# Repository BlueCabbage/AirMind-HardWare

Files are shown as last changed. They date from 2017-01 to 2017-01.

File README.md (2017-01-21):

Hardware
========



PX4 Hardware designs

Website at: http://pixhawk.org

PX4 is an open hardware design, following the OSHW 1.1 definition licensed under the Creative Commons Attribution-ShareAlike 3.0 Unported (CC BY-SA 3.0) license.

Pull requests for relevant fixes are very welcome.

Pixhawk v1 Hardware
===================

FMUv1 & FMUv2 boards

Design files are EAGLE CAD files (can be viewed with the free version)
www.cadsoftusa.com/

And BOM management is performed using Bob Starr's BOM-EX plugin:
http://www.bobstarr.net/pages/downloads.html

Pixhawk v2 Hardware
===================

FMUv3 board (and IMUv3 + PSMv3 support components)

The Pixhawk v2 Hardware is the result of a collaboration of the open hardware development community and 3D Robotics and has been designed in Altium.

MindPX V2 Hardware
===================

MindPX V2 board (Hardware version:   v2.2)
http://www.mindpx.net

Product brief:
http://www.mindpx.net/assets/accessories/brochure.pdf

Hardware specification:
http://www.mindpx.net/assets/accessories/Specification_MindPX.pdf

User manual:
http://www.mindpx.net/assets/accessories/UserGuide_MindPX.pdf

Revisions against Pixhawk:

1. 6 PWM distance sensors inputs
2. 1 extra parallel I2C port (so can support external compass and px4flow simultaneously)
3. Secondary USB port  for companion computer (converted from UART2 using onboard CP2104)
4. exposed SWD debug port
5. Built-in vibration dampening, support hard mount on air frames.
6. removed in v2.2:
        • Spektrum DSM / DSM2 / DSM-X® Satellite compatible input
        • Futaba S.BUS® compatible input and output
        • auxiliary outputs
        • safety switch (moved to power distribution board as eSwitch)

Note: MindPX v2.2 supports maximum 6 direct PWM outputs.

Creative Commons License Disclaimer
===================================

UNLESS OTHERWISE MUTUALLY AGREED TO BY THE PARTIES IN WRITING, LICENSOR OFFERS THE WORK AS-IS AND MAKES NO REPRESENTATIONS OR WARRANTIES OF ANY KIND CONCERNING THE WORK, EXPRESS, IMPLIED, STATUTORY OR OTHERWISE, INCLUDING, WITHOUT LIMITATION, WARRANTIES OF TITLE, MERCHANTIBILITY, FITNESS FOR A PARTICULAR PURPOSE, NONINFRINGEMENT, OR THE ABSENCE OF LATENT OR OTHER DEFECTS, ACCURACY, OR THE PRESENCE OF ABSENCE OF ERRORS, WHETHER OR NOT DISCOVERABLE. SOME JURISDICTIONS DO NOT ALLOW THE EXCLUSION OF IMPLIED WARRANTIES, SO SUCH EXCLUSION MAY NOT APPLY TO YOU.
EXCEPT TO THE EXTENT REQUIRED BY APPLICABLE LAW, IN NO EVENT WILL LICENSOR BE LIABLE TO YOU ON ANY LEGAL THEORY FOR ANY SPECIAL, INCIDENTAL, CONSEQUENTIAL, PUNITIVE OR EXEMPLARY DAMAGES ARISING OUT OF THIS LICENSE OR THE USE OF THE WORK, EVEN IF LICENSOR HAS BEEN ADVISED OF THE POSSIBILITY OF SUCH DAMAGES.

http://creativecommons.org/licenses/by-sa/3.0/

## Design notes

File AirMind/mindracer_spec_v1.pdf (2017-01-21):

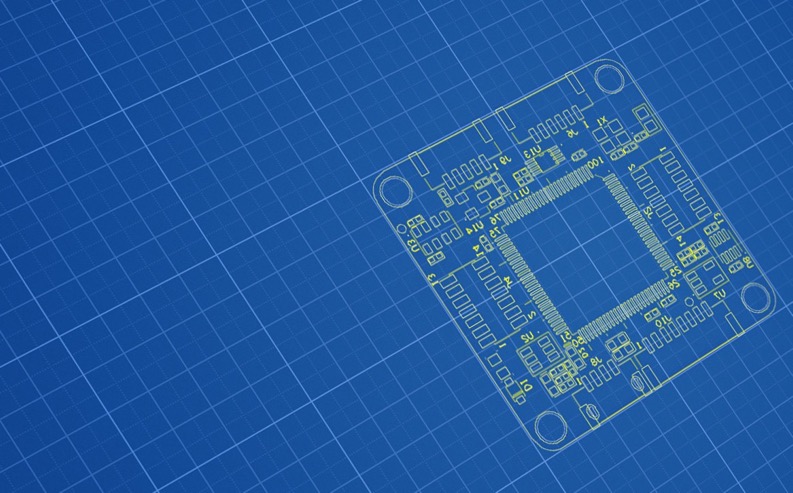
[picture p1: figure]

# MINDRACER

# SPECIFICATION

### Highlights

- Ultra mini size, weight only ~6g
- High performance F4 168MHz floating point processor, super fast throttle response
- Support OneShot ESC
- Support PPM/SBUS/DSM radio receivers, support D.Port/S.Port/Wifi telemetry
- On board flight data recorder
- Support IMU isolation
- DroneCode standard compliant connector

Website
www.mindpx.net

Contact
support@mindpx.net
V1.0 | AirMind Inc.,

Table of Content

Physical | 3
Power | 4
IMU | 5
Connectors | 5
Remote | 5
Telemetry | 5
Connectors pin out map | 5
Expansion ports | 7
Color LED Indicator | 8
Support | 8

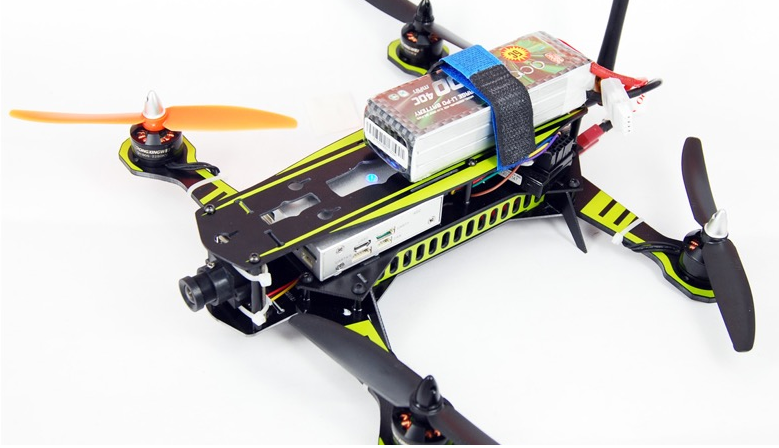
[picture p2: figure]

### Physical

| MindRacer
Flight controller / Processor | F427 VIT6
Weight | ~6g
Dimension | 35 x 35mm
PWM outputs | maximum 6
IMU | 10DOF
IMU isolation | YES/Optional
Radio receiver | PPM/S.BUS/SUMD/SPEKTRUM
Telemetry | FrSky D.Port, S.Port, Wifi, 3DR radio
on board TF card for flight data recording | YES
OneShot ESC support | YES
Expansion ports | 2 x 7(pin) x 2
on board Real time clock | YES
connector | JST GH (compliance with DroneCode standard)

### Power

Input voltage: 5V DC (+4.7V ~ +5.2 V, from PDB) Current: ~150ma (no peripheral)

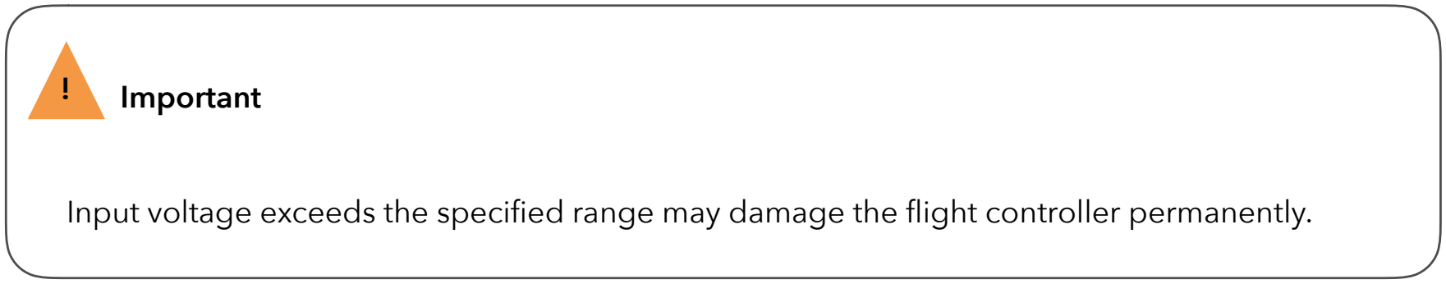
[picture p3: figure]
Important

Input voltage exceeds the specified range may damage the flight controller permanently.

MindRacer can powering small peripheral devices through its ports. MindRacer can provide 2 kind of voltage, +5V and +3.3V. Check MindRacer specification for the pin out of power supply.
MindRacer can supply maximum 100mA@5V or 100mA@3.3V.

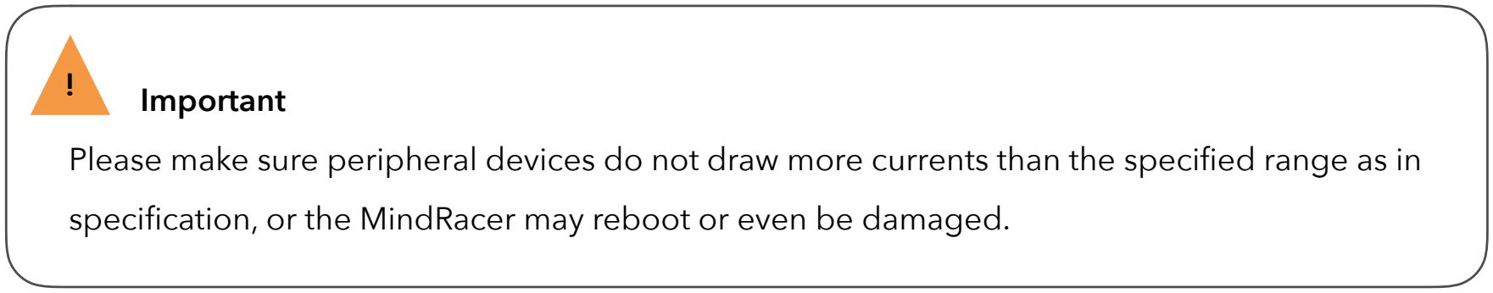
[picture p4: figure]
Important

Please make sure peripheral devices do not draw more currents than the specified range as in specification, or the MindRacer may reboot or even be damaged.

### IMU

On board IMU components include:

Accelerometer: MPU-6500
Gyroscope: MPU-6500
Compass: HMC5983
Barometer: MS5611

MindRacer supports the option to mount redundant, isolated IMUs through is on board connector.

### Connectors

J1 - USB (micro)
J3 - TF card slot
J7 - vibration isolated IMU interface
J15 - SWD/Serial 5
J8 - General purpose telemetry port (TELEM2) J9 - RC input
J10 - Main outputs
J13 - Power

### Remote

MindRacer supports PPM, S.BUS, SUMD, SPEKTRUM DSM/Satellite receivers through its one-wire serial remote control input port.
Spektrum satellite receiver use 3.3V output as power supply so a different cable is provided than other receivers.

### Telemetry

MindRacer supports 3DR radio and Wifi telemetry through its telemetry ports. MindRacer also provides support to FrySky D.Port and S.Port telemetry through its expansion ports (use a breakout board).

### Connectors pin out map

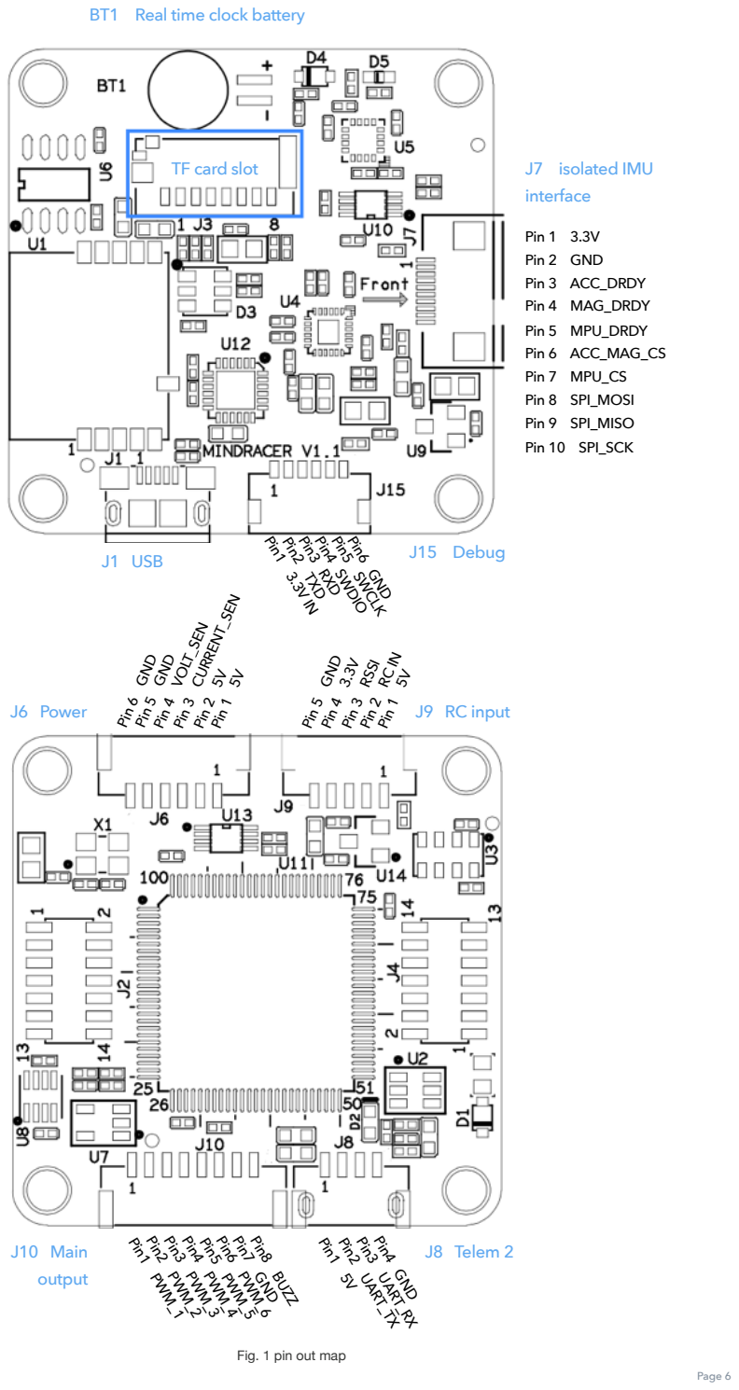
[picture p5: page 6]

Fig. 1 pin out map

Pin1 PWM_1

Pin2 PWM_2

Pin3 PWM_3

Pin4 PWM_4
Pin5 PWM_5

Pin6 PWM_6

Pin7 GND
Pin8 BUZZ
Pin1 5V

Pin2 UART_TX

Pin3 UART_RX

Pin4 GND

Pin 6 GND

Pin 5 GND

Pin 4 VOLT_SEN

Pin 3 CURRENT_SEN

Pin 2 5V

Pin 1 5V

Pin 5 GND
Pin 4 3.3V
Pin 3 RSSI

Pin 2 RC IN
Pin 1 5V
J6 Power | J9 RC input
J10 Main | J8 Telem 2
output
TF card slot | J7 isolated IMU interface
| Pin 1 3.3V Pin 2 GND Pin 3 ACC_DRDY Pin 4 MAG_DRDY Pin 5 MPU_DRDY Pin 6 ACC_MAG_CS Pin 7 MPU_CS Pin 8 SPI_MOSI Pin 9 SPI_MISO Pin 10 SPI_SCK

J15 Debug Pin1 3.3V IN
Pin2 TXD

Pin3 RXD
Pin4 SWDIO

Pin5 SWCLK

Pin6 GND
J1 USB

BT1 Real time clock battery

### Expansion ports

MindRacer has two 2x7 1.27mm pitch pin headers for port replication/expansion. The pin out map for the 2 expansion ports are defined as following.

J2 Sensor expansion port

Table 1 sensor expansion port pin out

J4 PWM expansion port

Table 2 PWM expansion port pin out

PIN # | Signal
| 1 BAT_VOLT_SEN
| 2 +5V
| 3 FMU_UART2_TX
| 4 BAT_CURRENT_SEN
| 5 CAN_L
| 6 FMU_UART2_RX
| 7 RSSI_IN
| 8 CAN_H
| 9 SPEAKER_OUT
| 10 RC_IN
| 11 FRSKY_IN (UART_RX)
| 12 V3.3_OUT
| 13 GND
| 14 FRSKY_OUT(UART_TX)
PIN # | Signal
| 1 FMU_UART4_TX
| 2 +5V
| 3 FMU_PWM_CH2
| 4 FMU_UART4_RX
| 5 FMU_PWM_CH4
| 6 FMU_PWM_CH1
| 7 FMU_PWM_CH6
| 8 FMU_PWM_CH3
| 9 USB_EXT_DM
| 10 FMU_PWM_CH5
| 11 FMU_I2C2_SDA
| 12 USB_EXT_DP
| 13 GND
| 14 FMU_I2C2_SCL

### Color LED Indicator

The main LED indicator is a tricolor LED and can show different status information with the combination of different colors and blinks. The status information it indicates is listed below:

Table 3 LED indicator

### Support

Please visit www.mindpx.org for more information. Or you can send email to support@mindpx.net for any inquiries or help.

LED color | meaning (status) | remark
Solid any color | Armed
Breathing any color | Standby
Amber | Low battery or Failsafe | (Return to home, etc)
Blue | GPS not locked
Green | GPS Locked
Fast Blink & Red | Arming error
Blink & Red | Other error
Transitional Green | Mode switch success

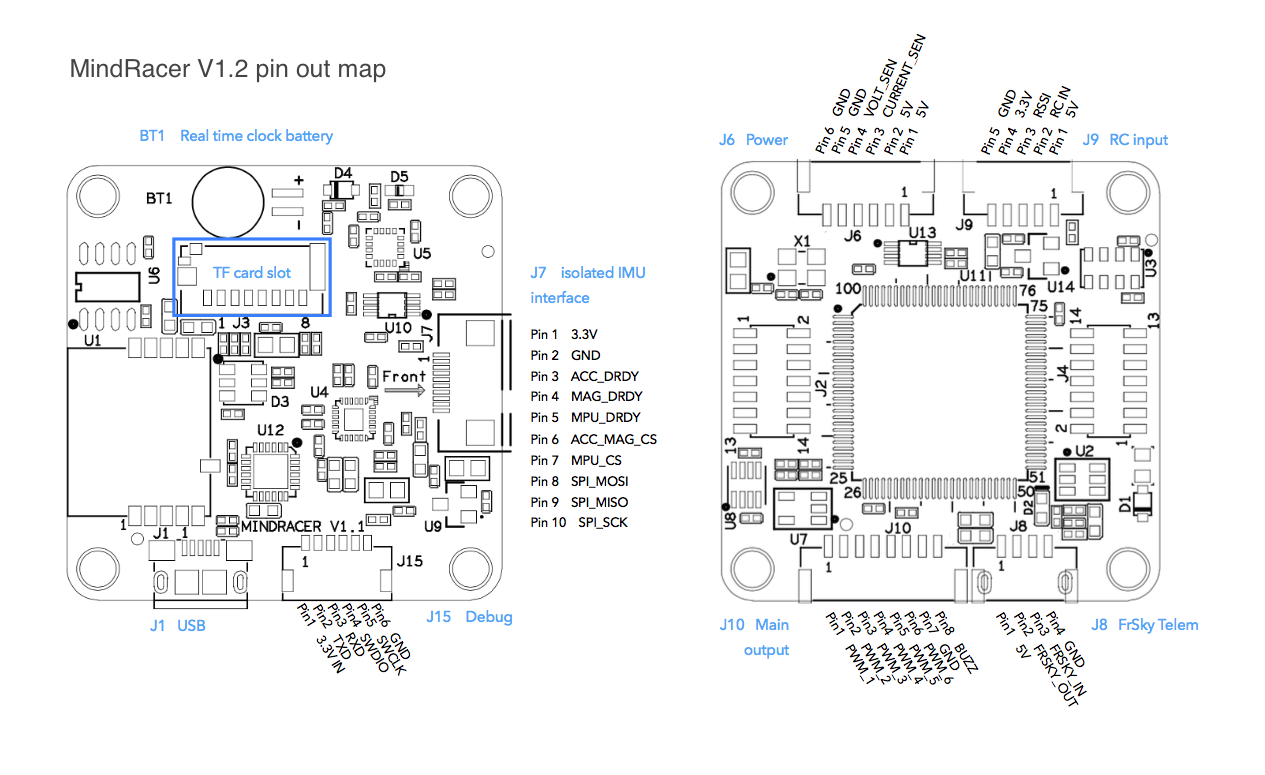
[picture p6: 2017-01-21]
AirMind/Mindracerv12pinmap.png

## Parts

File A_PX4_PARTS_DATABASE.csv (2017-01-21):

Mfg Part Num | Mfg Name | VID | Vendor Part Num | Description | Vendor Qty 1 | Vendor Qty 2 | Vendor Qty 3 | Customer Ref | Price Qty 1 | Price Qty 2 | Price Qty 3 | Vendor Reel Part Num | Vendor Link | Datasheet Link | VID2 | Vendor 2 Part Num | Vendor 2 Derivate Part Num | Vendor 2 Price Qty 1 | Vendor 2 Link
CC0402ZRY5V7BB104 | Yageo | DK | 311-1047-1-ND | CAP .10UF 16V CERAMIC Y5V 0402 | 10 | 100 | 500 |  | 0.011 | 0.0065 | 0.00376 | 311-1047-6-ND | http://search.digikey.com/scripts/DkSearch/dksus.dll?Detail&name=311-1047-1-ND | http://media.digikey.com/pdf/Data%20Sheets/Yageo%20PDFs/MLCC%20ordering%20code.pdf | ME | 81-GRM155R71C104KA88 | GRM155R71C104KA88D | 0.022 | http://at.mouser.com/ProductDetail/Murata/GRM155R71C104KA88D/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
F931A106MAA | Nichicon | DK | 493-2351-1-ND | CAP TANTALUM 10UF 10V 20% SMD | 10 | 100 | 250 |  | 0.349 | 0.21 | 0.15752 | 493-2351-6-ND | http://search.digikey.com/scripts/DkSearch/dksus.dll?Detail&name=493-2351-1-ND | http://products.nichicon.co.jp/en/pdf/XJA039/e-f93.pdf | ME | 80-B45196H2106K109 | B45196H2106K109 | 0.203 | http://at.mouser.com/ProductDetail/Kemet/B45196H2106K109/?qs=sGAEpiMZZMuEN2agSAc2pkTaD7b2aQjmQy5HG6VoQ2g%3d
MSS1P4-M3/89A | Vishay | DK | MSS1P4-M3/89AGICT-ND | DIODE SCHOTTKY 1A 40V MICROSMP | 10 | 100 | 250 |  | 0.326 | 0.1919 | 0.13576 | MSS1P4-M3/89AGIDKR-ND | http://search.digikey.com/scripts/DkSearch/dksus.dll?Detail&name=MSS1P4-M3/89AGICT-ND | http://www.vishay.com/docs/89019/mss1p4.pdf | ME | 625-MSS1P4-M3 | MSS1P4-M3/89A | 0.245 | http://at.mouser.com/ProductDetail/Vishay/MSS1P4-M3-89A/?qs=fLSHF8TigmUkO6GnwlXAxQ%3d%3d
953230-2000-AR-PR | 3M | DK | 3M9272CT-ND | CONN SOCKET 30POS 2MM VERT SMD | 1 | 100 |  |  | 3.22 | 2.449 |  | 3M9272DKR-ND | http://search.digikey.com/scripts/DkSearch/dksus.dll?Detail&name=3M9272CT-ND | http://multimedia.3m.com/mws/mediawebserver?mwsId=66666UuZjcFSLXTtmXMEm8T_EVuQEcuZgVs6EVs6E666666-- | ME | 517-953230-2000-ARPR | 953230-2000-AR-PR | 3.35 | http://at.mouser.com/ProductDetail/3M-Electronic-Solutions-Division/953230-2000-AR-TP/
47346-0001 | Molex Inc | DK | WM17141CT-ND | CONN RCPT 5POS MICRO USB R/A | 10 | 50 | 250 |  | 0.793 | 0.6612 | 0.54992 | WM17141DKR-ND | http://search.digikey.com/scripts/DkSearch/dksus.dll?Detail&name=WM17141DKR-ND | http://www.molex.com/pdm_docs/sd/473460001_sd.pdf | ME | 538-47346-0001 | 47346-0001 | 1.44 | http://at.mouser.com/ProductDetail/Molex/47346-0001/?qs=c2CV6XM0DweJBWaSeyWeCw%3d%3d
M50-3900542 | Harwin Inc | DK | 952-1395-ND | CONN HDR 1.27MM R/A AU 10POS | 10 | 50 | 100 |  | 1.242 | 1.035 | 0.92 |  | http://search.digikey.com/scripts/DkSearch/dksus.dll?vendor=0&keywords=M50-3900542 | http://www.harwin.com/include/downloads/pdfs/2010PAGE95.PDF | ME | 855-M50-3900542 | M50-3900542 | 0.968 | http://at.mouser.com/ProductDetail/Harwin/M50-3900542/?qs=9fQaSFfsqsyxvSF9FxJVZQ%3d%3d
L3G4200DH | STMicroelectronics | DK | 497-11071-1-ND | IC GYROSCOPE MEMS 3AXIS LP 16LGA | 10 | 100 | 250 |  | 12.39 | 10.62 | 9.73500 | 497-11071-6-ND | http://search.digikey.com/scripts/DkSearch/dksus.dll?Detail&name=497-11071-1-ND | http://www.st.com/stonline/products/literature/ds/17116.pdf | ME | 511-L3G4200D | L3G4200D | 12.41 | http://at.mouser.com/ProductDetail/STMicroelectronics/L3G4200D/?qs=sGAEpiMZZMtlZAfbtrLey%252by4mKX%2fvdEL
HMC5843 | HMC5843 | DK | 342-1071-1-ND | SENSOR MAGNETIC 3 AXIS 20-LCC | 1 | 100 | 500 |  | 20 | 17 | 15 | 342-1071-6-ND | http://search.digikey.com/scripts/DkSearch/dksus.dll?Detail&name=342-1071-1-ND | http://www.sparkfun.com/datasheets/Sensors/Magneto/HMC5843.pdf
BMP0805 | Bosch Sensortec | DK | 828-1005-1-ND | DIGITAL BAROMETRIC PRESSURE SNSR | 10 | 100 | 250 |  | 8.79 | 7.325 | 5.567 | 828-1005-6-ND | http://search.digikey.com/scripts/DkSearch/dksus.dll?Detail&name=828-1005-1-ND | http://www.bosch-sensortec.com/content/language1/downloads/BST-BMP085-DS000-05.pdf
LIS331DLH | STMicroelectronics | DK | 497-10397-1-ND | ACCELEROMETER MEMS 3AXIS 16-LGA | 10 | 100 | 250 |  | 8.316 | 6.93 | 6.237 | 497-10397-6-ND | http://search.digikey.com/scripts/DkSearch/dksus.dll?Detail&name=497-10397-1-ND | http://www.st.com/internet/com/TECHNICAL_RESOURCES/TECHNICAL_LITERATURE/DATASHEET/CD00213470.pdf | ME | 511-LIS331DLH | LIS331DLH | 7.87 | http://at.mouser.com/ProductDetail/STMicroelectronics/LIS331DLH/?qs=sGAEpiMZZMvAvBNgSS9Lql%252bnfyR4OMMz
24FC128-I/MS | Microchip | DK | 24FC128-I/MS-ND | IC EEPROM 128KBIT 1MHZ 8MSOP | 10 | 25 | 100 |  | 0.84 | 0.6 | 0.58 |  | http://search.digikey.com/scripts/DkSearch/dksus.dll?Detail&name=24FC128-I/MS-ND | http://ww1.microchip.com/downloads/en/DeviceDoc/21191s.pdf | ME | 579-24FC128-I/MS | 24FC128-I/MS | 0.639 | http://at.mouser.com/ProductDetail/Microchip/24FC128-I-MS/?qs=XNV0BZVlaZHXU0%2fvkIaqxQ%3d%3d
7M-16.000MEEQ-T | TXC | DK | 887-1319-1-ND | CRYSTAL 16.000 MHZ 10PF SMD | 10 | 50 | 100 |  | 1.463 | 1.2826 | 1.0125 | 887-1319-6-ND | http://search.digikey.com/scripts/DkSearch/dksus.dll?Detail&name=887-1319-1-ND | http://www.txccrystal.com/images/pdf/7m-accuracy.pdf | ME | 717-7M-16.000MEEQ-T | 7M-16.000MEEQ-T | 9999 | http://at.mouser.com/ProductDetail/TXC/7M-16000MEEQ-T/?qs=65dIHZNch5syu%2fvH9aFnbA%3d%3d
MIC5207-3.3YM5 | Micrel Inc | DK | 576-1267-1-ND | IC REG LDO 180MA 3.3V SOT23-5 | 1 | 100 | 250 |  | 1.02 | 0.85 | 0.51 | 576-1267-6-ND | http://search.digikey.com/scripts/DkSearch/dksus.dll?Detail&name=576-1267-1-ND | http://www.micrel.com/_PDF/mic5207.pdf
LD1117AS33 | STMicroelectronics | DK | 497-1228-1-ND | IC REG LDO 3.3V 1.2A SOT-223 | 10 | 100 | 250 |  | 0.84 | 0.663 | 0.5746 | 497-1228-6-ND | http://search.digikey.com/scripts/DkSearch/dksus.dll?Detail&name=497-1228-1-ND | http://www.st.com/internet/com/TECHNICAL_RESOURCES/TECHNICAL_LITERATURE/DATASHEET/CD00002116.pdf | ME | 511-LD1117AS33 | LD1117AS33TR | 0.477 | http://at.mouser.com/ProductDetail/STMicroelectronics/LD1117AS33TR/?qs=C3bf%2fVrkE5CoDDd7wyn%252baQ%3d%3d
EVQP7J01K | Panasonic - ECG | DK | P12278SCT-ND | SWITCH LT 3.5MMX2.9MM 160GF SMD | 10 | 100 | 500 |  | 0.734 | 0.6163 | 0.52826 | P12278SDKR-ND | http://search.digikey.com/scripts/DkSearch/dksus.dll?Detail&name=P12278SCT-ND | http://industrial.panasonic.com/www-data/pdf/ATK0000/ATK0000CE20.pdf
SN74LVC2T45 | Texas Instruments | DK | 296-17014-1-ND | Translator, Bidirectional, 3-State, 2bits | 1 | 25 | 100 |  | 0.79 | 0.612 | 0.54 | 296-17014-6-ND | http://search.digikey.com/scripts/DkSearch/dksus.dll?Detail&name=296-17014-1-ND | http://focus.ti.com/lit/ds/symlink/sn74lvc2t45.pdf | ME | 595-SN74LVC2T45DCUR | SN74LVC2T45DCUR | 0.766 | http://at.mouser.com/ProductDetail/Texas-Instruments/SN74LVC2T45DCUR/?qs=0smPjiIwnfIdG9vxyJHBdA%3d%3d
BKP1005HS121-T | Taiyo Yuden | DK | 587-1921-1-ND | FERRITE BEAD 120 OHM 0402 | 10 | 100 | 500 |  | 0.2 | 0.08 | 0.041 | 587-1921-6-ND | http://search.digikey.com/scripts/DkSearch/dksus.dll?Detail&name=587-1921-1-ND | http://www.yuden.co.jp/us/product/pdf/ebkp_e.pdf | ME | 81-BLM15PD121SN1D | BLM15PD121SN1D | 0.107 | http://at.mouser.com/ProductDetail/Murata/BLM15PD121SN1D/
BM06B-SRSS-TB | JST | DK | 455-1792-1-ND | CONN HEADER SH 6POS TOP 1MM TIN | 10 | 100 | 500 |  | 0.66 | 0.5504 | 0.4403 | 455-1792-6-ND | http://search.digikey.com/scripts/DkSearch/dksus.dll?Detail&name=455-1792-1-ND | http://www.jst-mfg.com/product/pdf/eng/eSH.pdf
GRM155F51C474ZA01D | Murata Electronics | DK | 490-3274-1-ND | CAP CER .47UF 16V Y5V 0402 | 10 | 100 | 500 |  | 0.044 | 0.026 | 0.015 | 490-3274-6-ND | http://search.digikey.com/scripts/DkSearch/dksus.dll?Detail&name=490-3274-1-ND | http://search.murata.co.jp/Ceramy/image/img/PDF/ENG/GRM155F51C474ZA01.pdf
53261-15 | Molex Inc | DK | WM7632CT-ND | CONN HEADER 15POS 1.25MM R/A SMD | 10 | 50 | 100 |  | 2.199 | 1.8992 | 1.6993 | WM7632DKR-ND | http://search.digikey.com/scripts/DkSearch/dksus.dll?Detail&name=WM7632CT-ND | http://www.molex.com/pdm_docs/sd/532611571_sd.pdf | ME | 538-53261-1571 | 53261-1571 | 3.79 | http://at.mouser.com/ProductDetail/Molex/53261-1571/?qs=sGAEpiMZZMticT%2fTNjssTkTynroYBL5J
CC0402KRX7R7BB103 | Yageo | DK | 311-1042-1-ND | CAP 10000PF 16V CERAMIC X7R 0402 | 10 | 100 | 500 |  | 0.011 | 0.0067 | 0.00386 | 311-1042-6-ND | http://search.digikey.com/scripts/DkSearch/dksus.dll?Detail&name=311-1042-1-ND | http://media.digikey.com/pdf/Data%20Sheets/Yageo%20PDFs/MLCC%20ordering%20code.pdf | ME | 810-C1005X7R1C103K | C1005X7R1C103K | 0.032 | http://at.mouser.com/ProductDetail/TDK/C1005X7R1C103K/?qs=sGAEpiMZZMvQvaS66kI3ToxS7c2J4e237rb4UXwcIBM%3d
C1005Y5V1C224Z | TDK Corporation | DK | 445-3444-1-ND | CAP CER .22UF 16V Y5V 0402 | 10 | 100 | 500 |  | 0.03 | 0.0176 | 0.01012 | 445-3444-6-ND | http://search.digikey.com/scripts/DkSearch/dksus.dll?Detail&name=445-3444-1-ND | http://www.tdk.com/pdf/general_A11.pdf
C1608Y5V0J475Z | TDK Corporation | DK | 445-3449-1-ND | CAP CER 4.7UF 6.3V Y5V 0603 | 10 | 100 | 500 |  | 0.121 | 0.0715 | 0.04126 | 445-3449-6-ND | http://search.digikey.com/scripts/DkSearch/dksus.dll?Detail&name=445-3449-1-ND | http://www.tdk.com/pdf/general_A11.pdf | ME | 810-C1608X5R0J475M | C1608X5R0J475M | 0.095 | http://at.mouser.com/ProductDetail/TDK/C1608X5R0J475M/
CC0402KRX7R9BB471 | Yageo | DK | 311-1028-1-ND | CAP 470PF 50V CERAMIC X7R 0402 | 10 | 100 | 500 |  | 0.011 | 0.0067 | 0.00386 | 311-1028-6-ND | http://search.digikey.com/scripts/DkSearch/dksus.dll?Detail&name=311-1028-1-ND | http://media.digikey.com/pdf/Data%20Sheets/Yageo%20PDFs/MLCC%20ordering%20code.pdf
TXB0102DCUR | Texas Instruments | DK | 296-22862-1-ND | IC VOLT-LVL TRANSL BI-DIR 8-US8 | 1 | 25 | 100 |  | 1.48 | 1.17 | 1.053 | 296-22862-6-ND | http://search.digikey.com/scripts/DkSearch/dksus.dll?Detail&name=296-22862-1-ND | http://focus.ti.com/lit/ds/symlink/txb0102.pdf | ME | 595-TXB0102DCUR | TXB0102DCUR | 1.55 | http://at.mouser.com/ProductDetail/Texas-Instruments/TXB0102DCUR/
MF-FSMF050X-2 | Bourns Inc. | DK | MF-FSMF050X-2CT-ND | FUSE PTC RESET 500MA SMD 0603 | 10 | 100 | 500 |  | 0.36 | 0.33 | 0.312 | MF-FSMF050X-2DKR-ND | http://search.digikey.com/scripts/DkSearch/dksus.dll?Detail&name=MF-FSMF050X-2CT-ND | http://www.bourns.com/data/global/pdfs/mffsmf.pdf | ME | 652-MFFSMF050X-2 | MF-FSMF050X-2 | 0.448 | http://at.mouser.com/ProductDetail/Bourns/MF-FSMF050X-2/?qs=3QkGRBNOvbrZekaW8Gqm4A%3d%3d
MF-FSMF020X-2 | Bourns Inc. | DK | MF-FSMF020X-2CT-ND | FUSE PTC RESET 200MA SMD 0603 | 10 | 100 | 500 |  | 0.36 | 0.33 | 0.312 | MF-FSMF020X-2DKR-ND | http://search.digikey.com/scripts/DkSearch/dksus.dll?Detail&name=MF-FSMF020X-2CT-ND | http://www.bourns.com/data/global/pdfs/mffsmf.pdf | ME | 652-MFFSMF020X-2 | MF-FSMF020X-2 | 0.448 | http://at.mouser.com/ProductDetail/Bourns/MF-FSMF020X-2/?qs=3QkGRBNOvbqaTWjqPUQNsg%3d%3d
C1608Y5V1C225Z | TDK Corporation | DK | 445-3451-1-ND | CAP CER 2.2UF 16V Y5V 0603 | 10 | 100 | 500 |  | 0.088 | 0.052 | 0.03 | 445-3451-6-ND | http://search.digikey.com/scripts/DkSearch/dksus.dll?Detail&name=445-3451-1-ND | http://www.tdk.com/pdf/general_A11.pdf | ME | 810-C1608Y5V1C225Z | C1608Y5V1C225Z | 0.085 | http://at.mouser.com/ProductDetail/TDK/C1608Y5V1C225Z/
CC0402JRNP09BN100 | Yageo | DK | 311-1014-1-ND | CAP CERAMIC 10PF 50V NP0 0402 | 10 | 100 | 500 |  | 0.012 | 0.007 | 0.00406 | 311-1014-6-ND | http://search.digikey.com/scripts/DkSearch/dksus.dll?Detail&name=311-1014-1-ND | http://www.yageo.com/documents/recent/UPY-GP_NP0_16V-to-50V_6.pdf | ME | 581-04023U100JAT2A | 04023U100JAT2A | 0.032 | http://at.mouser.com/ProductDetail/AVX/04023U100JAT2A/
RC0402FR-0739K2L | Yageo | DK | 311-39.2KLRCT-ND | RES 39.2K OHM 1/16W 1% 0402 SMD | 10 | 50 | 200 |  | 0.067 | 0.0362 | 0.02085 | 311-39.2KLRDKR-ND | http://search.digikey.com/scripts/DkSearch/dksus.dll?Detail&name=311-39.2KLRCT-ND | http://www.yageo.com/documents/recent/PYu-RC0402_51_RoHS_L_6.pdf | ME | 304-39.2K-RC | 304-39.2K-RC | 0.045 | http://at.mouser.com/ProductDetail/Xicon/304-392K-RC/?qs=sGAEpiMZZMtG0KNrPCHnjZ81IsZ41qnEdwGMvS7VK3o%3d
ERJ-2GEJ680X | Panasonic - ECG | DK | P68JCT-ND | RES 68 OHM 1/10W 5% 0402 SMD | 1 | 50 | 100 |  | 0.05 | 0.0172 | 0.0131 | P68JDKR-ND | http://search.digikey.com/scripts/DkSearch/dksus.dll?Detail&name=P68JCT-ND | http://industrial.panasonic.com/www-cgi/jvcr13pz.cgi?E+PZ+3+AOA0001+ERJ2GEJ680X+7+WW
CC0402ZRY5V7BB104 | TDK | ME | 810-C1005X7R1C104M | CAP .10UF 16V CERAMIC Y7R 0402 | 10 | 100 | 500 |  | 0.032 | 0.01 | 0.009 | 810-C1005X7R1C104M | http://at.mouser.com/ProductDetail/TDK/C1005X7R1C104M/?qs=sGAEpiMZZMvQvaS66kI3Ts8kcYAvnUrc2X3P8fTRlAY%3d | http://media.digikey.com/pdf/Data%20Sheets/Yageo%20PDFs/MLCC%20ordering%20code.pdf
SM06B-SRSS-TB | JST | DK | 455-1806-1-ND | CONN HEADER SH 6POS SIDE 1MM TIN | 10 | 100 | 500 |  | 0.653 | 0.5445 | 0.4356 | 455-1806-6-ND | http://search.digikey.com/scripts/DkSearch/dksus.dll?Detail&name=455-1806-1-ND | http://www.jst-mfg.com/product/pdf/eng/eSH.pdf
ABM3B-8.000MHZ-10-1-U-T | Abracon Corporation | DK | 535-9721-1-ND | CRYSTAL 8.000 MHZ 10PF SMD | 10 | 50 | 100 |  | 2.048 | 1.7956 | 1.4175 | 535-9721-6-ND | http://search.digikey.com/scripts/DkSearch/dksus.dll?Detail&name=535-9721-1-ND | http://www.abracon.com/Resonators/abm3b.pdf | ME | 815-ABM3B-8.0-B2-T | ABM3B-8.000MHZ-B2-T | 1.01 | http://at.mouser.com/ProductDetail/ABRACON/ABM3B-8000MHZ-B2-T/?qs=NE97hfUNX0Ef9OqIOqO2cA%3d%3d
STM32F100C6T6B | STMicroelectronics | DK | 497-10500-ND | MCU 32BIT ARM 32K FLASH 48LQFP | 10 | 100 | 250 |  | 2.55 | 2.091 | 1.887 |  | http://search.digikey.com/scripts/DkSearch/dksus.dll?Detail&name=497-10500-ND | http://www.st.com/internet/com/TECHNICAL_RESOURCES/TECHNICAL_LITERATURE/DATASHEET/CD00251732.pdf | ME | 511-STM32F100C6T6B | STM32F100C6T6B | 2.77 | http://at.mouser.com/ProductDetail/STMicroelectronics/STM32F100C6T6B/?qs=sGAEpiMZZMs%2f2%2fdgfKIueKwtjHOoM53O
PTH08080WAH | Texas Instruments | DK | 296-20432-ND | MODULE PIP .9-5.5V 2.25A HORZ TH | 1 | 25 | 100 |  | 10.75 | 8.8152 | 7.955 |  | http://search.digikey.com/scripts/DkSearch/dksus.dll?vendor=0&keywords=PTH08080WAH&stock=1 | http://focus.ti.com/lit/ds/symlink/pth08080w.pdf | ME | 595-PTH08080WAH | PTH08080WAH | 11.3 | http://at.mouser.com/ProductDetail/Texas-Instruments/PTH08080WAH/?qs=sGAEpiMZZMuo%252bmZx5g6tFE82QReiwhO7
53047-02 | Molex Inc | DK | WM1731-ND | CONN HEADER 2POS 1.25MM VERT TIN | 50 | 100 | 250 |  | 0.2778 | 0.2395 | 0.21076 |  | http://search.digikey.com/scripts/DkSearch/dksus.dll?WT.z_header=search_go&lang=en&site=us&x=0&y=0 | http://www.molex.com/pdm_docs/sd/530470210_sd.pdf
53047-03 | Molex Inc | DK | WM1732-ND | CONN HEADER 3POS 1.25MM VERT TIN | 50 | 100 | 250 |  | 0.342 | 0.2948 | 0.2594 |  | http://search.digikey.com/scripts/DkSearch/dksus.dll?WT.z_header=search_go&lang=en&site=us&x=0&y=0 | http://www.molex.com/pdm_docs/sd/530470310_sd.pdf
53047-04 | Molex Inc | DK | WM1733-ND | CONN HEADER 4POS 1.25MM VERT TIN | 50 | 100 | 250 |  | 0.378 | 0.329 | 0.28 |  | http://search.digikey.com/scripts/DkSearch/dksus.dll?WT.z_header=search_go&lang=en&site=us&x=0&y=0 | http://www.molex.com/pdm_docs/sd/530470410_sd.pdf
53047-05 | Molex Inc | DK | WM1734-ND | CONN HEADER 5POS 1.25MM VERT TIN | 50 | 100 | 250 |  | 0.4816 | 0.4192 | 0.3568 |  | http://search.digikey.com/scripts/DkSearch/dksus.dll?WT.z_header=search_go&lang=en&site=us&x=0&y=0 | http://www.molex.com/pdm_docs/sd/530470510_sd.pdf
T491X107K025ZT | Kemet | DK | 399-5175-1-ND | CAP TANT 100UF 25V 10% SMD | 10 | 25 | 100 |  | 2.453 | 2.3448 | 2.1645 | 399-5175-6-ND | http://search.digikey.com/scripts/DkSearch/dksus.dll?Detail&name=399-5175-1-ND | http://www.kemet.com/datasheets&T491X107K025ZT
T491A475K010AT | Kemet | DK | 399-3696-1-ND | CAPACITOR TANT 4.7UF 10V 10% SMD | 10 | 100 | 250 |  | 0.349 | 0.21 | 0.15752 | 399-3696-6-ND | http://search.digikey.com/scripts/DkSearch/dksus.dll?Detail&name=399-3696-1-ND | http://www.kemet.com/datasheets&T491A475K010AT
TC164-JR-07100RL | Yageo | DK | TC164J-100CT-ND | RES ARRAY 100 OHM 8TRM 4 RES SMD | 10 | 100 | 500 |  | 0.012 | 0.0103 | 0.00736 | TC164J-100DKR-ND | http://search.digikey.com/scripts/DkSearch/dksus.dll?Detail&name=TC164J-100CT-ND | http://www.yageo.com/documents/recent/PYu-YC_TC164_51_RoHS_L_3.pdf
SN74LVC8T245DBQR | Texas Instruments | DK | 296-23279-1-ND | IC BUS TRANSCVR 8BIT 24QSOP | 1 | 25 | 100 |  | 1.33 | 1.05 | 0.945 | 296-23279-6-ND | http://search.digikey.com/scripts/DkSearch/dksus.dll?Detail&name=296-23279-1-ND | http://focus.ti.com/lit/ds/symlink/sn74lvc8t245.pdf
S3B-ZR-SM4A-TF | JST | DK | 455-1694-1-ND | CONN HEADER ZH SIDE 3POS 1.5MM | 1 | 10 | 100 |  | 0.56 | 0.516 | 0.43 | 455-1694-6-ND | http://search.digikey.com/scripts/DkSearch/dksus.dll?Detail&name=455-1694-1-ND
TLP3123(F) | Toshiba | DK | TLP3123F-ND | PHOTORELAY MOSFET 1A 4-SOP | 10 | 100 | 250 |  | 3.15 | 2.45 | 2.32752 |  | http://search.digikey.com/scripts/DkSearch/dksus.dll?WT.z_header=search_go&lang=en&site=us&x=0&y=0 | http://www.semicon.toshiba.co.jp/docs/datasheet/en/Opto/TLP3123_en_datasheet_071001.pdf
AP2151WG-7 | Diodes Inc | DK | AP2151WGDICT-ND | IC PWR SW USB 1CH 0.5A SOT-25-5 | 10 | 100 | 250 |  | 0.855 | 0.675 | 0.585 |  | http://search.digikey.com/scripts/DkSearch/dksus.dll?Detail&name=AP2151WGDICT-ND | http://www.diodes.com/datasheets/AP2141_51.pdf
74LVC2GU04GW,125 | NXP Semiconductors | DK | 568-4843-1-ND | IC DUAL INVERTER SC88-6 | 1 | 25 | 100 |  | 0.52 | 0.3428 | 0.2816 | 568-4843-6-ND | http://search.digikey.com/scripts/DkSearch/dksus.dll?Detail&name=568-4843-1-ND | http://www.nxp.com/documents/data_sheet/74LVC2GU04.pdf | ME | 771-LVC2GU04GW125 | 74LVC2GU04GW,125 | 0.577 | http://ch.mouser.com:80/Search/ProductDetail.aspx
MAX3051ESA+ | Maxim Integrated Products | DK | MAX3051ESA+-ND | IC TXRX CAN 1MBPS 8-SOIC | 1 | 25 | 100 |  | 2.56 | 1.71 | 1.24 |  | http://search.digikey.com/scripts/DkSearch/dksus.dll?Detail&name=MAX3051ESA%2B-ND | http://datasheets.maxim-ic.com/en/ds/MAX3051.pdf
DF12C(3.0)-50DS-0.5V | Hirose Electric Co Ltd | DK | DF12C(3.0)-50DS-0.5V(81)-ND | CONN RECEPT 50 POS SMD 0.5MM | 1000 |  |  |  | 0.8379 |  |  |  | http://search.digikey.com/scripts/DkSearch/dksus.dll?WT.z_header=search_go&lang=en&site=us&x=0&y=0 | http://www.hirose.co.jp/cataloge_hp/e53700036.pdf
B4B-PH-K | JST | DK | 455-1706-ND | CONN HEADER PH TOP 4POS 2MM | 10 | 100 | 500 |  | 0.11122 | 0.167 | 0.139 |  | http://search.digikey.com/scripts/DkSearch/dksus.dll?vendor=0&keywords=B4B-PH-K-S&stock=1 | http://www.jst-mfg.com/product/pdf/eng/ePH.pdf
S02B-PASK-2 | JST | DK | 455-1847-ND | CONN HEADER PA 2POS SIDE 2MM TIN | 10 | 100 | 500 |  | 0.225 | 0.1872 | 0.14974 |  | http://search.digikey.com/scripts/DkSearch/dksus.dll?vendor=0&keywords=S02B-PASK-2&stock=1 | http://www.jst-mfg.com/product/pdf/eng/ePA-F.pdf
B3B-ZR | JST | DK | 455-1658-ND | CONN HEADER ZH TOP 3POS 1.5MM | 10 | 100 | 500 |  | 0.123 | 0.1028 | 0.08222 | 455-1682-6-ND | http://search.digikey.com/scripts/DkSearch/dksus.dll?Detail&name=455-1658-ND | http://www.jst-mfg.com/product/pdf/eng/eZH.pdf
53261-03 | Molex Inc | DK | WM7621CT-ND | CONN HEADER 3POS 1.25MM R/A SMD | 10 | 50 | 100 |  | 1.09 | 0.9082 | 0.8173 | WM7621DKR-ND | http://search.digikey.com/scripts/DkSearch/dksus.dll?Detail&name=WM7621CT-ND | http://www.molex.com/pdm_docs/sd/532610371_sd.pdf
53261-04 | Molex Inc | DK | WM7622CT-ND | CONN HEADER 4POS 1.25MM R/A SMD | 10 | 50 | 100 |  | 1.193 | 0.994 | 0.8946 | WM7622DKR-ND | http://search.digikey.com/scripts/DkSearch/dksus.dll?Detail&name=WM7622CT-ND | http://www.molex.com/pdm_docs/sd/532610471_sd.pdf
P120JCT-ND | Panasonic - ECG | DK | P120JCT-ND | RES 120 OHM 1/10W 5% 0402 SMD | 1 | 50 | 100 |  | 0.05 | 0.0172 | 0.0131 | P120JDKR-ND | http://search.digikey.com/scripts/DkSearch/dksus.dll?Detail&name=P120JCT-ND | http://industrial.panasonic.com/www-cgi/jvcr13pz.cgi?E+PZ+3+AOA0001+ERJ2GEJ121X+7+WW
ERJ-2RKF3570X | Panasonic - ECG | DK | P357LCT-ND | RES 357 OHM 1/10W 1% 0402 SMD | 1 | 50 | 100 |  | 0.06 | 0.0242 | 0.0184 | P357LDKR-ND | http://search.digikey.com/scripts/DkSearch/dksus.dll?Detail&name=P357LCT-ND | http://industrial.panasonic.com/www-cgi/jvcr13pz.cgi?E+PZ+3+AOA0002+ERJ2RKF3570X+7+WW
AMIS42673ICAG1RG | ON Semiconductor | DK | 766-1008-1-ND | TRANSCEIVER CAN HS 3.3V 8-SOIC | 1 | 100 | 250 |  | 2.38 | 1.666 | 1.496 | 766-1008-6-ND | http://search.digikey.com/scripts/DkSearch/dksus.dll?Detail&name=766-1008-1-ND | http://www.onsemi.com/pub_link/Collateral/AMIS-42673-D.PDF
STM32F103C4T6A | STMicroelectronics | DK | 497-8316-ND | MCU ARM 32BIT 16K FLASH 48-LQFP | 10 | 100 | 250 |  | 5.85 | 4.81 | 4.42 |  | http://search.digikey.com/scripts/DkSearch/dksus.dll?Detail&name=497-8316-ND | http://www.st.com/internet/com/TECHNICAL_RESOURCES/TECHNICAL_LITERATURE/DATASHEET/CD00210843.pdf
STM32F102C6T6A | STMicroelectronics | DK | 497-8306-ND | MCU ARM 32BIT 32KB FLASH 48-LQFP | 10 | 100 | 250 |  | 5.67 | 4.662 | 4.284 |  | http://search.digikey.com/scripts/DkSearch/dksus.dll?Detail&name=497-8306-ND | http://www.st.com/internet/com/TECHNICAL_RESOURCES/TECHNICAL_LITERATURE/DATASHEET/CD00210833.pdf
LNJ337W83RA | Panasonic - SSG | DK | LNJ337W83RACT-ND | LED GREEN HIGH BRIGHT ESS SMD | 1 | 25 | 100 |  | 0.53 | 0.31 | 0.25 | LNJ337W83RADKR-ND | http://search.digikey.com/scripts/DkSearch/dksus.dll?Detail&name=LNJ337W83RACT-ND | http://industrial.panasonic.com/www-cgi/jvcr13pz.cgi?E+SC+4+ATA7003+LNJ337W83RA+8+WW
HMC5883L | Honeywell | DK | 342-1082-1-ND | IC COMPASS 3 AXIS I2C 16LCC SMD | 1 | 25 | 100 |  | 3.79 | 2.2356 | 1.8829 | 342-1082-6-ND | http://search.digikey.com/scripts/DkSearch/dksus.dll?Detail&name=342-1082-1-ND | http://media.digikey.com/PDF/Data%20Sheets/Honeywell%20PDFs/HMC5883L.pdf
STM32F205 | STMicroelectronics | DK | 497-11157-ND | MCU ARM 1024KB FLASH 64LQFP | 1 | 25 | 100 |  | 15.38 | 12.9316 | 11.883 |  | http://search.digikey.com/scripts/DkSearch/dksus.dll?lang=en&site=US&KeyWords=stm32f205rgt6&x=0&y=0 | http://www.st.com/internet/com/TECHNICAL_RESOURCES/TECHNICAL_LITERATURE/DATASHEET/CD00237391.pdf
951230-2520-AR-PR | 3M | DK | 3M9197CT-ND | CONN HEADER 30POS 2MM VERT SMD | 1 | 100 |  |  | 2.2 | 1.6748 |  |  | http://search.digikey.com/scripts/DkSearch/dksus.dll?Detail&name=3M9197CT-ND | http://multimedia.3m.com/mws/mediawebserver?66666UuZjcFSLXTtmxTXmXfEEVuQEcuZgVs6EVs6E666666-- | ME | 538-87759-3050 | 87759-3050 | 5.4 | http://ch.mouser.com:80/ProductDetail/Molex/87759-3050/?qs=sGAEpiMZZMtsLRyDR9nM10M7wAK5dulTwNabOIeF5lA%3d
ERJ-2RKF2050X | Panasonic - ECG | DK | P205LCT-ND | RES 205 OHM 1/10W 1% 0402 SMD | 1 | 50 | 100 |  | 0.06 | 0.0242 | 0.0184 | P205LDKR-ND | http://search.digikey.com/scripts/DkSearch/dksus.dll?Detail&name=P205LCT-ND | http://industrial.panasonic.com/www-cgi/jvcr13pz.cgi?E+PZ+3+AOA0002+ERJ2RKF2050X+7+WW
NTGS4111P | ON Semiconductor | DK | NTGS4111PT1G | MOSFET P-CH 30V 2.6A 6-TSOP | 10 | 100 | 250 |  | 0.445 | 0.3042 | 0.25352 | NTGS4111PT1GOSDKR-ND | http://search.digikey.com/scripts/DkSearch/dksus.dll?Detail&name=NTGS4111PT1GOSCT-ND | http://www.onsemi.com/pub_link/Collateral/NTGS4111P-D.PDF
NX3225SA-24.000000MHZ | NDK | DK | NX3225SA-24.000000MHZ | CRYSTAL 24.000000 MHZ 8PF SMD | 10 | 50 | 100 |  | 0.92 | 0.8064 | 0.6367 | 644-1052-6-ND | http://search.digikey.com/scripts/DkSearch/dksus.dll?Detail&name=644-1052-1-ND | http://media.digikey.com/pdf/Data%20Sheets/NDK%20PDFs/NX3225SA.pdf | ME | 815-ABM8G-24-18-D2Y | ABM8G-24.000MHZ-18-D2Y-T | 1.79 | http://at.mouser.com:80/ProductDetail/ABRACON/ABM8G-24000MHZ-18-D2Y-T/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
FT4232HL | FTDI | DK | 768-1026-1-ND | IC USB HS QUAD UART/SYNC 64-LQFP | 10 | 50 | 100 |  | 8.66 | 8.1 | 6.84 | 768-1026-6-ND | http://search.digikey.com/scripts/DkSearch/dksus.dll?Detail&name=768-1026-1-ND | http://www.ftdichip.com/Support/Documents/DataSheets/ICs/DS_FT4232H.pdf
7M-12.000MEEQ-T | TXC CORPORATION | DK | 887-1316-1-ND | CRYSTAL 12.000 MHZ 10PF SMD | 10 | 50 | 100 |  | 1.463 | 1.2826 | 1.0125 | 887-1316-6-ND | http://search.digikey.com/scripts/DkSearch/dksus.dll?Detail&name=887-1316-1-ND | http://www.txccrystal.com/images/pdf/7m-accuracy.pdf
MMS1208 | APEM Components, LLC | DK | 679-1854-ND | SWITCH MICRO-MINI SLIDE | 10 | 50 | 100 |  | 1.003 | 0.85 | 0.765 |  | http://search.digikey.com/scripts/DkSearch/dksus.dll?WT.z_header=search_go&lang=en&site=us&x=0&y=0 | http://www.apem.com/pdf/MMS_MICRO_SLIDE.pdf
TS3A24157 | Texas Instruments | DK | 296-22856-1-ND | IC SWITCH DUAL SPDT 10MSOP | 1 | 25 | 100 |  | 1.41 | 1.11 | 0.999 | 296-22856-6-ND | http://search.digikey.com/scripts/DkSearch/dksus.dll?Detail&name=296-22856-1-ND | http://focus.ti.com/lit/ds/symlink/ts3a24157.pdf
UX60SC-MB-5ST(80) | Hirose Electric Co Ltd | DK | H11671CT-ND | CONN RCPT USB MINI B R/A SMD | 10 | 25 | 100 |  | 0.62 | 0.55 | 0.45 | H11671DKR-ND | http://search.digikey.com/scripts/DkSearch/dksus.dll?Detail&name=H11671CT-ND | http://www.hirose.co.jp/cataloge_hp/e24000153.pdf
EVQ-5PN04K | Panasonic - ECG | DK | P13595SCT-ND | SWITCH LT TOUCH 6X3.5 240GF SMD | 10 | 100 | 500 |  | 0.513 | 0.4309 | 0.36936 | P13595SDKR-ND | http://search.digikey.com/scripts/DkSearch/dksus.dll?Detail&name=P13595SCT-ND | http://industrial.panasonic.com/www-data/pdf/ATK0000/ATK0000CE7.pdf
SBH11-PBPC-D10-RA-BK | Sullins Connector Solutions | DK | S9180-ND | CONN HEADR 2.54MM 20POS GOLD R/A | 1 | 25 | 100 |  | 0.76 | 0.6888 | 0.4879 |  | http://search.digikey.com/scripts/DkSearch/dksus.dll?Detail&name=S9180-ND | http://www.sullinscorp.com/drawings/145_SBH11-PBPC-D___-RA-___,_11092-B.pdf
XG4C-3031 | Omron Electronics Inc-EMC Div | DK | OR994-ND | CONN PLUG 30POS 3A 300V STRT DIP | 1 | 25 | 100 |  | 1.61 | 1.4468 | 1.1576 |  | http://search.digikey.com/scripts/DkSearch/dksus.dll?Detail&name=OR994-ND | http://components.omron.com/components/web/pdflib.nsf/0/1D642D622E2FDCF685257201007DD590/$file/XG4_1110.pdf
68000-406HLF | FCI | DK | 609-3263-ND | CONN HEADER 6POS .100 STR TIN | 1 | 25 | 100 |  | 0.37 | 0.1744 | 0.1352 |  | http://search.digikey.com/scripts/DkSearch/dksus.dll?Detail&name=609-3263-ND | http://portal.fciconnect.com/res/en/pdffiles/doc_search/68000.pdf
93LC46BT-I/ST | Microchip Technology | DK | 93LC46BT-I/STCT-ND | IC EEPROM 1KBIT 2MHZ 8TSSOP | 10 | 25 | 100 |  | 0.26 | 0.25 | 0.24 | 93LC46BT-I/STDKR-ND | http://search.digikey.com/scripts/DkSearch/dksus.dll?Detail&name=93LC46BT-I/STCT-ND | http://ww1.microchip.com/downloads/en/DeviceDoc/21749H.pdf
TXS0102DCUR | Texas Instruments | DK | 296-21931-1-ND | IC VOLT-LEVEL TRANSLATOR 8-US8 | 1 | 25 | 100 |  | 1.25 | 0.99 | 0.891 | 296-21931-6-ND | http://search.digikey.com/scripts/DkSearch/dksus.dll?Detail&name=296-21931-1-ND | http://focus.ti.com/lit/ds/symlink/txs0102.pdf
STM32F100C8T6B | STMicroelectronics | DK | 497-10499-ND | MCU 32BIT ARM 64K FLASH 48LQFP | 10 | 100 | 250 |  | 3.425 | 2.8085 | 2.53452 |  | http://search.digikey.com/scripts/DkSearch/dksus.dll?Detail&name=497-10499-ND | http://www.st.com/internet/com/TECHNICAL_RESOURCES/TECHNICAL_LITERATURE/DATASHEET/CD00251732.pdf
BAT 60A E6327 | Infineon Technologies | DK | BAT60AE6327INCT-ND | DIODE SCHOTTKY 10V 3A SOD-323 | 10 | 100 | 500 |  | 0.38300 | 0.25550 | 0.14820 | BAT60AE6327INDKR-ND | http://search.digikey.com/scripts/DkSearch/dksus.dll?Detail&name=BAT60AE6327INCT-ND | http://www.infineon.com/dgdl/bat60aseries.pdf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
BLM15HD102SN1 | Murata Electronics | DK | 490-4003-1-ND | FILTER CHIP 1000 OHM 250MA 0402 | 10 | 50 | 100 |  | 0.41500 | 0.27340 | 0.21680 | 490-4003-6-ND | http://search.digikey.com/scripts/DkSearch/dksus.dll?Detail&name=490-4003-1-ND | http://search.murata.co.jp/Ceramy/image/img/PDF/ENG/L0110S0101BLM15H.pdf
STM32F405RGT6 | STMicroelectronics | DK | 497-11767-ND | IC MCU 168 MHZ FPU 32BIT 1MB FLASH 64LQFP | 10 | 100 | 250 |  | 13.08800 | 11.12460 | 10.14300 |  | http://search.digikey.com/us/en/products/STM32F405RGT6/497-11767-ND/2754208 | http://www.st.com/internet/com/TECHNICAL_RESOURCES/TECHNICAL_LITERATURE/DATASHEET/DM00037051.pdf
RC0402FR-0747KL | Yageo | DK | 311-47.0KLRCT-ND | RES 47.0K OHM 1/16W 1% 0402 SMD | 10 | 50 | 100 |  | 0.01400 | 0.01040 | 0.00790 | 311-47.0KLRDKR-ND | http://search.digikey.com/us/en/products/RC0402FR-0747KL/311-47.0KLRCT-ND/729563 | http://www.yageo.com/documents/recent/PYu-RC0402_51_RoHS_L_6.pdf
DF13-3P-1.25H(20) | Hirose Electric Co Ltd | DK | H2220-ND | CONN HEADER 3POS 1.25MM R/A TIN | 10 | 50 | 1000 |  | 0.49000 | 0.37800 | 0.18900 |  | http://search.digikey.com/us/en/products/DF13-3P-1.25H(20)/H2220-ND/241793 | http://www.hirose.co.jp/cataloge_hp/e53600014.pdf
DF13-2P-1.25DSA | Hirose Electric Co Ltd | DK | H2191-ND | CONN HEADER 2POS 1.25MM STR TIN | 10 | 50 | 1000 |  | 0.31300 | 0.20880 | 0.10080 |  | http://search.digikey.com/us/en/products/DF13-2P-1.25DSA/H2191-ND/241765 | http://www.hirose.co.jp/cataloge_hp/e53600014.pdf
DF13-4P-1.25DSA | Hirose Electric Co Ltd | DK | H2193-ND | CONN HEADER 4POS 1.25MM STR TIN | 10 | 50 | 1000 |  | 0.39900 | 0.30780 | 0.15390 |  | http://search.digikey.com/us/en/products/DF13-4P-1.25DSA/H2193-ND/241767 | http://www.hirose.co.jp/cataloge_hp/e53600014.pdf
DF13-4P-1.25H(20) | Hirose Electric Co Ltd | DK | H2221-ND | CONN HEADER 4POS 1.25MM R/A TIN | 10 | 50 | 1000 |  | 0.52700 | 0.42500 | 0.22610 | DF13-4P-1.25H(21)-ND | http://search.digikey.com/us/en/products/DF13-4P-1.25H(20)/H2221-ND/241794 | http://www.hirose.co.jp/cataloge_hp/e53600014.pdf
DF13-3P-1.25DSA | Hirose Electric Co Ltd | DK | H2192-ND | CONN HEADER 3POS 1.25MM STR TIN | 10 | 50 | 1000 |  | 0.30500 | 0.23500 | 0.11745 |  | http://search.digikey.com/us/en/products/DF13-3P-1.25DSA/H2192-ND/241766 | http://www.hirose.co.jp/cataloge_hp/e53600014.pdf
DF13A-3P-1.25H(20) | Hirose Electric Co Ltd | DK | H3368-ND | CONN HEADER 3POS 1.25MM R/A TIN | 10 | 50 | 1000 |  | 0.49000 | 0.37800 | 0.18900 |  | http://search.digikey.com/us/en/products/DF13A-3P-1.25H(20)/H3368-ND/530665 | http://www.hirose.co.jp/cataloge_hp/e53600014.pdf
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

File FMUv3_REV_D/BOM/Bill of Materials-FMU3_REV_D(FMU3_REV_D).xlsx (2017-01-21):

Manufacturer 1 | Manufacturer Part Number 1 | Description | Designator | Value | Quantity | Footprint
Yageo | CC0402ZRY5V7BB104 | CAP CER 0.1UF 16V Y5V 0402 | C1001, C3001, C3002, C3003, C3004, C4003, C4005, C4006, C5001, C5005, C5007, C5009, C5010, C5011, C5012, C5014, C5015, C7001, C7002, C7003, C7006, C8001, C8002, C8003, C10002 | 0u1 | 25 | 0402-CAP
TDK Corporation | C1005C0G1H080C050BA | CAP CER 8PF 50V C0G 0402 | C1002, C1003, C7004, C7005 | 8p | 4 | 0402-CAP
TDK Corporation | C1608X6S1C225K080AC | CAP CER 2.2UF 16V 10% X6S 0603 | C4001, C4002, C5013, C5016 | 2u2 | 4 | 0603-CAP
AVX Corporation | 06033C103JAT2A | CAP CER 10000PF 25V 5% X7R 0603 | C4004 | 0u01 | 1 | 0603-CAP
TDK Corporation | C1005X6S1E224K050BC | CAP CER 0.22UF 25V 10% X7R 0402 | C4007 | 0u22 | 1 | 0402-CAP
Samsung Electro-Mechanics America, Inc | CL21B475KOFNNNE | CAP CER 4.7UF 16V 10% X7R 0805 | C4008 | 4u7 | 1 | 0805
Samsung Electro-Mechanics America, Inc | CL21A106KAYNNNE | CAP CER 10UF 25V 10% X5R 0805 | C5002, C10001 | 10u/25 | 2 | 0805-CAP
Yageo | CC0402KRX7R7BB103 | CAP CER 10000PF 16V 10% X7R 0402 | C5003, C10003 | 10n | 2 | 0402-CAP
Yageo | CC0603ZRY5V7BB105 | CAP CER 1UF 16V Y5V 0603 | C5004, C10005 | 1u | 2 | 0603-CAP
Samsung Electro-Mechanics America, Inc | CL21A226MAQNNNE | CAP CER 22UF 25V 20% X5R 0805 | C5006, C5008 | 22u/25V | 2 | 0805-CAP
Murata Electronics North America | GRM21BR60G107ME15L |  | C5100, C5101 | 100uF | 2 | C0805
TDK Corporation | C1608X5R1A106K080AC | CAP CER 10UF 10V 10% X5R 0603 | C10004 | 10u | 1 | 0603-CAP
ON Semiconductor | RB751V40T1G | DIODE SCHOTTKY 30V 0.03A SOD323 | D5001 | 30V | 1 | SOD323
TE Connectivity / Raychem | PESD0402-140 | TVS DIODE 14VWM 40VC 0402 | D8001, D8002 | 40v | 2 | 0402-TVS
NXP Semiconductors | PMEG2005CT,215 | DIODE SCHOTTKY 20V 500MA TO236AB | D10001 | 20V | 1 | SOT23-3
Bel Fuse Inc | 0ZCA0035FF2G | PTC RESTTBLE 0.35A 16V CHIP 1206 | F10001 | 0.35A | 1 | PTC-1206
Molex Inc | 0473460001 | MICRO USB B, BOTTOM MOUNT | J2001 |  | 1 | MOLEX-47346-0001
AVX Corp/Kyocera Corp | KNH16C104DA5TS | FILTER CAP 0.1UF 2A 25V 0603 | L2001, L2002, L5001 | 0u1 | 3 | KYOCERA-KNH16-DA
Kingbright | APTD1608CGCK | LED GREEN ROUND CLEAR SMD | LED1, LED2, LED6001, LED6002, LED6003, LED6004, LED6005, LED6006, LED6007, LED6008, LED6009 | GREEN | 11 | 0603-LED-Blue
Kingbright | APTD1608SECK/J4-PF | LED 1.6X0.8 DOME ORN CLEAR SMD | LED6010, LED6011 | AMBER | 2 | 0603-LED
Infineon Technologies | MMBT 3906 LT1 | TRANSISTOR SWITCHING PNP SOT-23 | Q5001 |  | 1 | SOT23-BEC
Diodes Incorporated | BSS123-7-F | MOSFET N-CH 100V 170MA SOT23-3 | Q6001 | 100V | 1 | SOT23
Yageo | RC0402FR-07220RL | RES 220 OHM 1/16W 1% 0402 SMD | R1, R2, R1022, R4001, R4002, R6003, R6004, R6005, R6006, R6007, R6008, R6009, R6010, R6011, R6012, R6013, R6014, R6015, R7003, R7004, R7010, R7011, R7012 | 220R | 23 | 0402-RES
Yageo | RC0402FR-07470RL | RES 470 OHM 1/16W 1% 0402 SMD | R1001 | 470R | 1 | 0402-RES
Yageo | RC0402FR-0710KL | RES 10K OHM 1/16W 1% 0402 SMD | R1002, R5001, R5006, R6002, R7001, R7002, R8001 | 10K | 7 | 0402-RES
Panasonic Electronic Components | ERA-2AEB103X | RES 10K OHM 1/16W .1% 0402 SMD | R2001, R2002 | 10K | 2 | 0402-RES
Yageo | RC0402FR-071ML | RES 1M OHM 1/16W 1% 0402 SMD | R2003, R2004 | 1M | 2 | 0402-RES
Yageo | RC0402FR-071K5L | RES 1.5K OHM 1/16W 1% 0402 SMD | R3001, R3002, R3003, R3004, R6017 | 1K5 | 5 | 0402-RES
Yageo | RC0402FR-07120RL | RES 120 OHM 1/16W 1% 0402 SMD | R3005, R3006, R3007, R3008, R3009, R3010 | 120R | 6 | 0402-RES
Samsung Electro-Mechanics America, Inc | RC1005F182CS | RES 1.8K OHM 1/16W 1% 0402 | R5002 | 1K8 | 1 | 0402-RES
Samsung Electro-Mechanics America, Inc | RC1608J100CS | RES 10 OHM 1/10W 5% 0603 | R5003 | 10R | 1 | 0603-RES
Samsung Electro-Mechanics America, Inc | RC1005F102CS | RES 1K OHM 1/16W 1% 0402 | R5005, R6001 | 1K | 2 | 0402-RES
Panasonic | ERJ-2GEJ680X | Thick Film Resistors - SMD 0402 68ohms 5% Tol | R6016 | 68R | 1 | 0402-RES
Yageo | RC0402FR-07100KL | RES 100K OHM 1/16W 1% 0402 SMD | R10001 | 100K | 1 | 0402-RES
Panasonic Electronic Components | EXB-2HV104JV | RES ARRAY 100K OHM 8 RES 1506 | RN2001 | 100K | 1 | EXB2HV
Panasonic Electronic Components | EXB-2HV103JV | RES ARRAY 10K OHM 8 RES 1506 | RN2002 | 10K | 1 | EXB2HV
Panasonic Electronic Components | EXB-2HV121JV | RES ARRAY 120 OHM 8 RES 1506 | RN3001, RN3002, RN8001, RN8002 | 120R | 4 | EXB2HV
STMicroelectronics | STM32F427VIT6 | REV 3 Silicon or later IC MCU ARM 2MB FLASH 100LQFP | U1001 |  | 1 | TQFP100
Cypress Semiconductor Corp | FM25V01-G | IC FRAM 128KBIT 40MHZ 8SOIC | U1002 | 128k | 1 | SO08
ON Semiconductor | NUF2042XV6T1G | IC FILTER USB ESD PROTECT SOT363 | U2001 |  | 1 | SOT563-6
3M | 2908-05WB-MG | CONN MICRO SD CARD PUSH-PUSH R/A | U2002 |  | 1 | MICROSD
Texas Instruments | TXS0108ERGYR | IC XLATR VOLT-LVL 8B BDIR 20QFN | U3001, U3002, U8001, U8002 |  | 4 | QFN20-RGY
Maxim Integrated | MAX3051EKA+T | IC TXRX CAN 1MBPS SOT23-8 | U3003, U3004 | CAN | 2 | SOT23-8
InvenSense | MPU-6000 | GYRO/ACCELEROMETER 6AXIS 24QFN | U4001 |  | 1 | QFN-24
Honeywell Microelectronics & Precision Sensors | HMC5983-TR | IC COMPASS 3 AXIS 16-LCC | U4002 |  | 1 | HMC5983-new
Measurement Specialties, Inc. | MS561101BA03-50 | Board Mount Pressure Sensors | U4003 | 10-1200mbar | 1 | MS5611-01BA
Micrel Inc | MIC5332-SSYMT TR | IC REG LDO 3.3V 0.3A 8TMLF | U5001, U10002 | 3.3V | 2 | MLF-8-EPAD
STMicroelectronics | STM32F100C8T6B | MCU 32BIT ARM 64K FLASH 48LQFP | U7001 |  | 1 | TQFP48
NXP Semiconductors | 74LVC2G240DP,125 | IC INVERTER DUAL 4-INPUT 8TSSOP | U8003 | INV | 1 | TSSOP8_SOT505-2
Texas Instruments | BQ24313DSGT | IC LI+ CHARGER FRONT END 8-SON | U10001 |  | 1 | QFN8-DSG
Hirose Electric Co Ltd | DF40C(2.0)-20DS-0.4V(51) | CONN RCPT 20POS 0.4MM SMD GOLD | U$2 |  | 1 | DF-40C-20DS
Hirose Electric Co Ltd | DF17(3.0H)-80DS-0.5V(57) | CONN RECEPT 80POS .5MM SMD W/FIT | U$9001 |  | 1 | CON-DF17-80F
NDK | NX3225SA-24.000MHZ-STD-CSR-1 | CRYSTAL 24MHZ 8PF SMD | X1001, X7001 | 24MHz | 2 | OSCILLATOR-3.2X2.5

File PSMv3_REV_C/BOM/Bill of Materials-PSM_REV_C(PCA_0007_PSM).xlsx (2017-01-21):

Manufacturer 1 | Manufacturer Part Number 1 | Description | Designator | Value | Quantity | Footprint
Yageo | CC0402KRX7R7BB103 | CAP CER 10000PF 16V 10% X7R 0402 | C1 | 10N | 1 | 0402-CAP
Samsung Electro-Mechanics America, Inc | CL21A106KAYNNNE | CAP CER 10UF 25V 10% X5R 0805 | C2 | 10UF | 1 | 0805-CAP
Yageo | CC0603ZRY5V7BB105 | CAP CER 1UF 16V Y5V 0603 | C3, C7 | 1U | 2 | 0603-CAP
TDK Corporation | C1608X5R1A106K080AC | CAP CER 10UF 10V 10% X5R 0603 | C4, C401, C402 | 10U | 3 | 0603-CAP
Yageo | CC0402ZRY5V7BB104 | CAP CER 0.1UF 16V Y5V 0402 | C5 | 0U1 | 1 | 0402-CAP
TDK Corporation | C1005X5R1C474K050BC | CAP CER 0.47UF 16V 10% X5R 0402 | C6 | 0U47 | 1 | 0402-CAP
Kemet | C0402C562K5RACTU | CAP CER 5600PF 50V 10% X7R 0402 | C8 | 5N6 | 1 | 0402-CAP
TDK Corporation | C3216X5R1A107M160AC | CAP CER 100UF 10V 20% X5R 1206 | C801, C803, C805, C810 | 100U | 4 | 1206-CAP
Kemet | C0402C100J3GACTU | CAP CER 10PF 25V 5% NP0 0402 | C802, C804 | 10P | 2 | 0402-CAP
Murata Electronics North America | GRM1555C1E102JA01D | CAP CER 1000PF 25V 5% NP0 0402 | C806 | 1000P | 1 | 0402-CAP
TDK Corporation | C1005X7R1E104K050BB | CAP CER 0.1UF 25V 10% X7R 0402 | C807, C808, C809 | 0U1 | 3 | 0402-CAP
NXP Semiconductors | PMEG2005CT,215 | DIODE SCHOTTKY 20V 500MA TO236AB | D1, D3 | 20V | 2 | SOT23-3
ON Semiconductor | MMSZ5232BT1G | DIODE ZENER 5.6V 500MW SOD123 | D4 | 5.6V | 1 | SOD-123
Bel Fuse Inc | 0ZCA0035FF2G | PTC RESTTBLE 0.35A 16V CHIP 1206 | F1, F3 | 0.35A | 2 | PTC-1206
Bel Fuse Inc | 0ZCA0020FF2E | PTC RESTTBLE 0.20A 30V CHIP 1206 | F4 | 0.2A | 1 | PTC-1206
TDK Corporation | MLZ2012M470WTD25 | FIXED IND 47UH 170MA 4.81 OHM | L1 | 47UH | 1 | 0805-IND
AVX Corp/Kyocera Corp | KNH16C104DA5TS | FILTER CAP 0.1UF 2A 25V 0603 | L603 | 0U1 | 1 | KYOCERA-KNH16-DA
Micro Commercial Co | MMBT3906-TP | TRANS SS PNP 40V 300MW SOT23 | Q5001 | 40V | 1 | SOT23-BEC
Stackpole Electronics Inc | RMCF0402FT453K | RES 453K OHM 1/16W 1% 0402 | R1, R801, R804, R807 | 453K | 4 | 0402-RES
Stackpole Electronics Inc | RMCF0402FT16K5 | RES 16.5K OHM 1/16W 1% 0402 | R2, R401, R10001 | 16K5 | 3 | 0402-RES
Yageo | RC0402FR-07100KL | RES 100K OHM 1/16W 1% 0402 SMD | R3 | 100K | 1 | 0402-RES
Yageo | RC0402FR-0710KL | RES 10K OHM 1/16W 1% 0402 SMD | R4, R404 | 10K | 2 | 0402-RES
Stackpole Electronics Inc | RMCF0402FT9K09 | RES 9.09K OHM 1/16W 1% 0402 | R5 | 9K09 | 1 | 0402-RES
Yageo | RC0402FR-071ML | RES 1M OHM 1/16W 1% 0402 SMD | R402, R405 | 1M | 2 | 0402-RES
Stackpole Electronics Inc | RMCF0402FT25K5 | RES 25.5K OHM 1/16W 1% 0402 | R403 | 25K5 | 1 | 0402-RES
Panasonic Electronic Components | ERA-2AEB563X | RES 56K OHM 1/16W .1% 0402 SMD | R802, R805, R808 | 5.6K | 3 | 0402-RES
Panasonic Electronic Components | ERJ-2RKF1053X | RES 105K OHM 1/10W 1% 0402 SMD | R803, R806, R809 | 105K | 3 | 0402-RES
Samsung Electro-Mechanics America, Inc | RC1005F102CS | RES 1K OHM 1/16W 1% 0402 | R5002 | 1K | 1 | 0402-RES
Panasonic Electronic Components | EXB-28V105JX | RES ARRAY 1M OHM 4 RES 0804 | RN801 | 1M | 1 | EXB28V
Micrel Inc | MIC5332-SSYMT TR | IC REG LDO 3.3V 0.3A 8TMLF | U1 | 3.3V | 1 | MLF-8-EPAD
Linear Technology | LT3469ETS8#TRMPBF | IC AMP DVR W/REG 1.3MHZ TSOT23-8 | U2 | BUZZER | 1 | SOT23-8
Texas Instruments | BQ24315DSGT | IC LI+ CHARGER FRONT END 8SON | U401, U402 | 3.3V-30V | 2 | QFN8-DSG
ON Semiconductor | NTHD4102PT1G | MOSFET 2P-CH 20V 2.9A CHIPFET | U801, U802, U804 | 20V 2.9A | 3 | 1206-8
Linear Technology | LTC4417IUF#PBF | IC OR CTRLR SRC SELECT 24QFN | U803 | 3:1 | 1 | MO-220
Texas Instruments | BQ24313DSGT | IC LI+ CHARGER FRONT END 8-SON | U10001 | 3.3V-30V | 1 | QFN8-DSG
 |  |  |  | Total Qty. | 60
 |  |  |  | APPROVALS
PART NUMBER (3DR ERP) | BOM REVISION | REF. DRAWING/SCHEMATIC: |  | Dept. | Name | Signature
PCA_0007_PSM |  | PSM_REV_C.PrjPcb |  | Design Engineering (PR)
PRODUCT DESCRIPTION | ECR/ECO/ECN |  |  | Dir. Of Eng. | Tim M.
PSM_REV_C.PrjPcb |  | N/A |  | Operations Mgmt | Lorenzo L.
Total parts = | 60 | N/A |  | Production | Juan V.
Feeder requirement: | N/A | N/A

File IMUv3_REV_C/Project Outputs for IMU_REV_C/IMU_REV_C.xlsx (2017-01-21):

Manufacturer 1 | Manufacturer Part Number 1 | Description | Designator | Value | Quantity | Footprint
Yageo | CC0805ZKY5V6BB106 | Capacitor, 10uF, 10V, Y5V, 0805, Ceramic | C1, C4, C6, C13 | 10u | 4 | 0805-CAP
Yageo | CC0402ZRY5V7BB104 | Capacitor, 0.1uF, 16V, Y5V, 0402, Ceramic | C2, C5, C10, C12, C14 | 0u1 | 5 | 0402-CAP
Yageo | CC0402KRX7R7BB103 | Capacitor, 10000pF, 16V, 10%, X7R, 0402, Ceramic | C3 | 10000pF | 1 | 0402-CAP
TDK Corporation | C1005X5R1C474K050BC | Capacitor, 0.47uF, 16V, 10%, X5R, 0402, Ceramic | C7 | 0u47 | 1 | 0402-CAP
TDK Corporation | C1608X6S1C225K080AC | Capacitor, 2.2uF, 16V, 10%, X6S, 0603, Ceramic | C8, C9 | 2u2 | 2 | 0603-CAP
AVX Corporation | 06033C103JAT2A | Capacitor, 10000pF, 25V, 5%, X7R, 0603, Ceramic | C11 | 10000pF | 1 | 0603-CAP
PennEngineering | PEM-SMTSO-M1.6-2-ET | Fastener, M1.6x2mm, SMTSO, Carbon Steel | Nut 1, Nut 2, Nut 3, Nut 4 |  | 4 | PEM-SMTSO-M1.6-2-ET
Hirose Electric Co Ltd | DF40C-20DP-0.4V(51) | Connector, HDR, 20Pos, 0.4mm, SMD, GOLD | P1 | DF40C-20DP-0.4V(51) | 1 | DF40C-20-DP
STMICROELECTRONICS | L3GD20 | Sensor, Low-power, Three-axis, Angular rate | U1 |  | 1 | L3GD20
STMicroelectronics | LSM303DTR | Module, 3D Accelerometer, 3D Magnetometer | U2 |  | 1 | LSM303D
InvenSense | MPU-6000 | 3 Axis Accel, 3Axis Gyro | U3 |  | 1 | QFN-24
Measurement Specialties, Inc. | MS561101BA03-50 | Board, Digital pressure sensor I2C/SPI | U4 |  | 1 | MS5611-01BA

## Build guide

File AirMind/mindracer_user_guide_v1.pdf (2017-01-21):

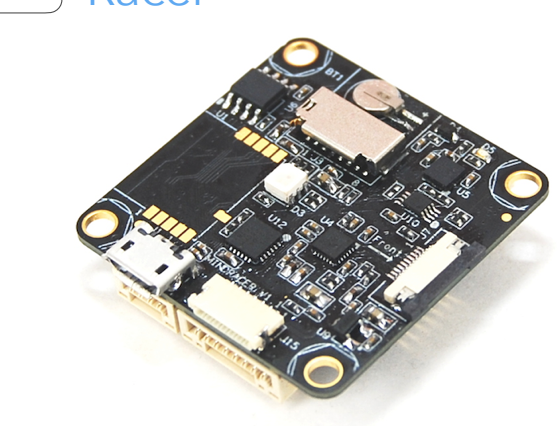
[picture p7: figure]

# MINDRACER

# USER MANUAL

### Highlights

- Ultra mini size, weight only ~6g
- High performance F4 168MHz floating point processor, super fast throttle response
- Support OneShot ESC
- Support PPM/SBUS/DSM radio receivers, support D.Port/S.Port/Wifi telemetry
- On board flight data recorder
- Support IMU isolation
- DroneCode standard compliant connector

Website
www.mindpx.net

Contact
support@mindpx.net

AirMind Inc.,

# MindPX

T h e U l t i m a t e

# Racer

## Quick self check

Before mounting please perform following quick check for any potential damages to MindRacer during logistic:
1. Check if any pin headers on the rear are bended or contacted
2. Check if the enclosed case is broken or damaged
3. Check if accessories are intact

If any situation above, please contact your local sales representatives for replacement.

## In package list

1. MindRacer main board
2. 3M tape
3. heat sink
4. cable set: FrSky telemetry cable, power cable, debug cable, main output cable, RC input cable, usb cable
5. racing breakout board


Table of Content

Physical | 4
Power | 4
Mounting | 5
Wiring | 8
On board Connectors | 11
Remote | 11
Calibration | 11
Connect to Ground Station | 11
Select Flight Mode | 13
Arm/Disarm | 14
Flight Black Box - Using a SD Card | 15
OSD | 15
The interface breakout board | 15
Telemetry | 16
Connect a GPS | 17
Color LED Indicator | 17
Support | 18

### Physical

### Power

MindRacer can be powered through its power port. The input voltage must be within the range from +4.7V ~ +5.2 V.
MindRacer can also be powered using an USB cable. This is usually the case when it is connected to the ground station for configuration or calibration.

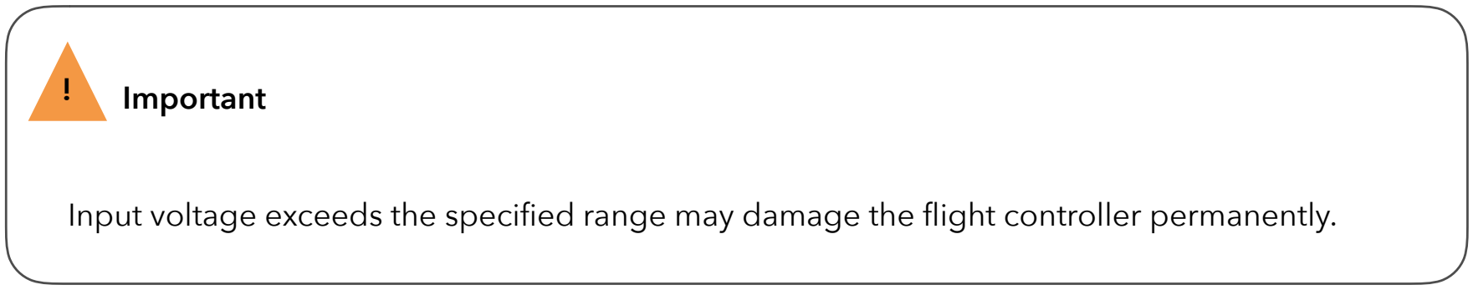
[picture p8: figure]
Important

Input voltage exceeds the specified range may damage the flight controller permanently.

| MindRacer
Flight controller / Processor | F427 VIT6
Weight | ~6g
Dimension | 35 x 35mm
PWM outputs | maximum 6
IMU | 10DOF
IMU isolation | YES/Optional
Radio receiver | PPM/SBUS/SPEKTRUM DSM/Satellite
Telemetry | FrSky D.Port, S.Port, Wifi, 3DR radio
on board TF card for flight data recording | YES
OneShot ESC support | YES
Expansion slots | 2 x 7(pin) x 2
on board Real time clock | YES
connector | JST GH (compliance with DroneCode standard)

MindRacer can powering small peripheral devices through its ports. MindRacer can provide 2 kind of voltage, +5V and +3.3V. Check MindRacer specification for the pin out of power supply.
MindRacer can supply maximum 100mA@5V or 100mA@3.3V.

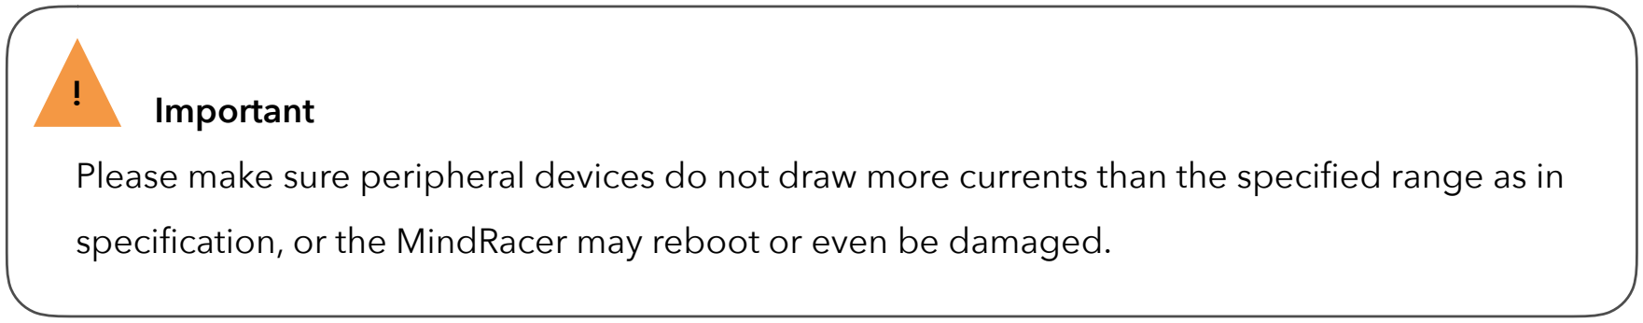
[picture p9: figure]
Important

Please make sure peripheral devices do not draw more currents than the specified range as in specification, or the MindRacer may reboot or even be damaged.

### Mounting

Direction of head
Before mounting, please make sure the head direction of MindRacer board(see the ‘front’ direction mark) is consistent with the head direction of airframe.

There are 2 ways of mounting your MindRacer onto your airframe,
1) heat sink mount
2) header pin mount

Heat sink mount
Heat sink is a piece of processed metal can be mounted on the bottom side of MindRacer. You can directly adhere the MindRacer with heat sink together onto the supporting carbon board of airframe using 3M tape. The 3M tape should be attached to the bottom side of the heat sink.
Heat sink mount is a very flexible mounting method with minimum weight, extremely suite-able for cases like racing match or irregular airframe.

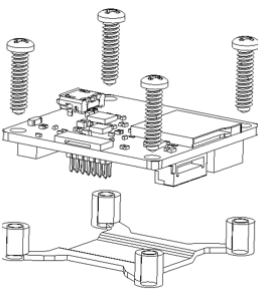
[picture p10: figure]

Fig. 1 heat sink mount

Header pin mount
MindRacer can also be mounted into a base PDB board through its 2 header pins on the bottom side. In this mounting method MindRacer’s ports are led out through the header pins to the PDB boards, so that pilots can utilize most features out of MindRacer.
Header pin mounting requires a PDB board with matching female headers. This PDB board can be obtained from AirMind website, or you can download the open PCB files to made yourself.
Header pin mounting can lead to a very clean build of copter - most of wiring has gone through the header pins so in rare case you need to jump wires. Only peripheral devices may need further wiring.

IMU isolation mount
Though has a complete set of IMUs on board, MindRacer can support a redundant set of IMUs in an isolated and vibration dampening rack.
The isolated mounting rack can help reduce the impact of vibration and improve the flight performance. The rack can be mounted directly on MindRacer board through 4 mounting hole using M3 screws.

* If you use barometer during flight, please use a piece of foam to cover on the surface of it (on the corner of bottom side of the board).

### heat sink

### flight controller

### screws

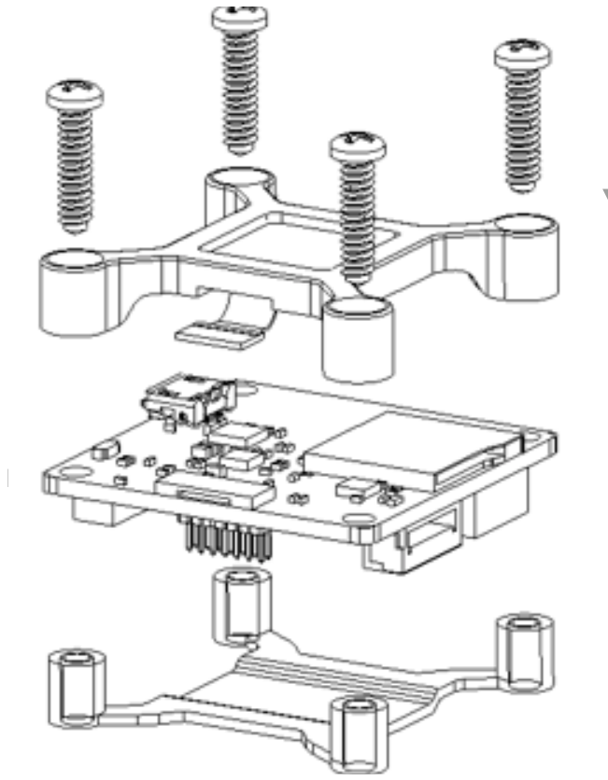
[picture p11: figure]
Fig. 1 quick install

Fig. 2 IMU isolation mount

PDB (power distribution board) mount

MindRacer mounts even perfectly when using specially designed PDB. Although MindRacer is compatible with other PDBs, using MRPDB is soldering-free, and can result in a very clean mount with minimum wiring for safer racing.
The MRPDB (the ‘fishbone’) is a power distribution board specially designed for racing frames, with female pins right matching MindRacer’s pin headers. MindRacer’s PWM outputs are routed to the MRPDB’s specially designed ESC ports, making connecting to ESCs is soldering-free, very fast and clean.

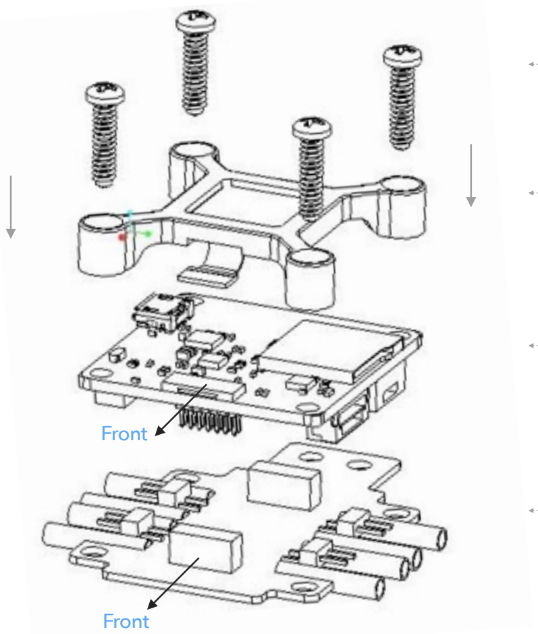
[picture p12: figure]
Front

Fig. 3 MRPDB mount

### heat sink

### flight controller

### screws

### IMU isolation rack

### flight controller

### screws

### IMU isolation rack

### MRPDB

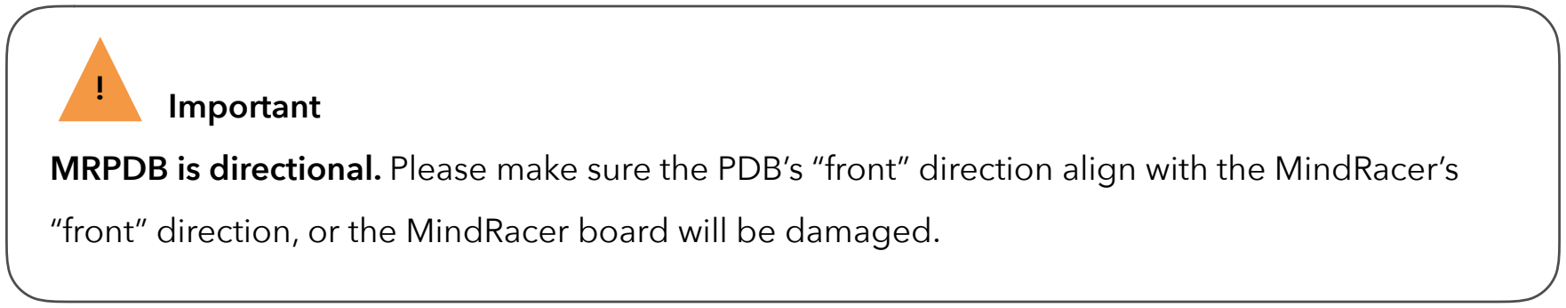
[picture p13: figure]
Important

MRPDB is directional. Please make sure the PDB’s “front” direction align with the MindRacer’s “front” direction, or the MindRacer board will be damaged.

### Wiring

The wiring methods can be little different depending on the airframe you choose. The most important thing is motor mapping that ensure the copter will fly correctly.
MindRacer’s motor mapping is shown as following map. The digital numbers map to MindRacer’s output pin number.

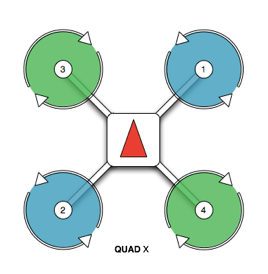
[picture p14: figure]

Fig. 4 Quad X motor map

Below is a real mounting & wiring case. Wire the MindRacer’s PWM output pin to corresponding numbered ESC/motor.

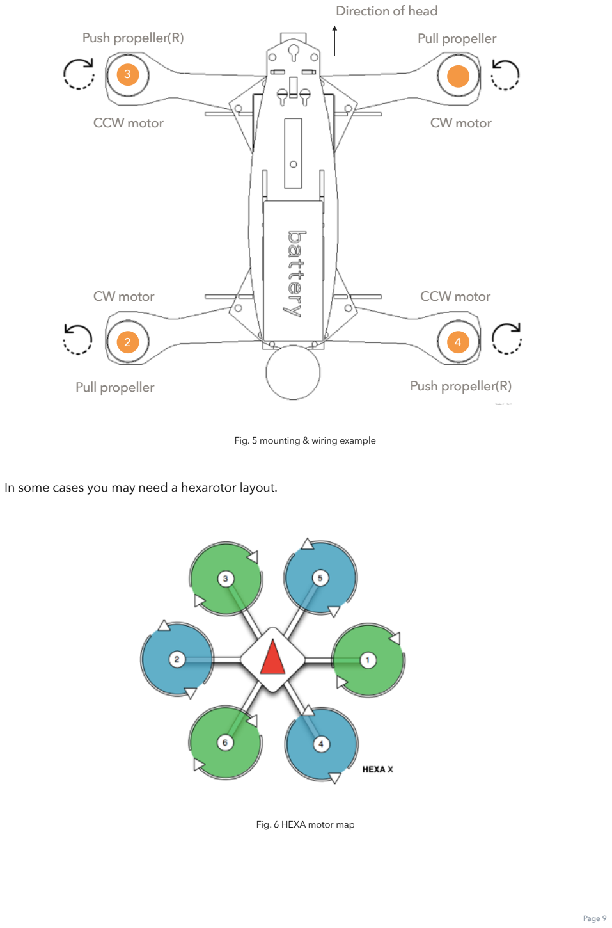
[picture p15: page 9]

Fig. 5 mounting & wiring example

In some cases you may need a hexarotor layout.

Fig. 6 HEXA motor map

2

3

4

CCW motor | CW motor
Push propeller(R) | Pull propeller
Pull propeller | Push propeller(R)
CW motor | CCW motor

Direction of head

Heat sink mounting wiring

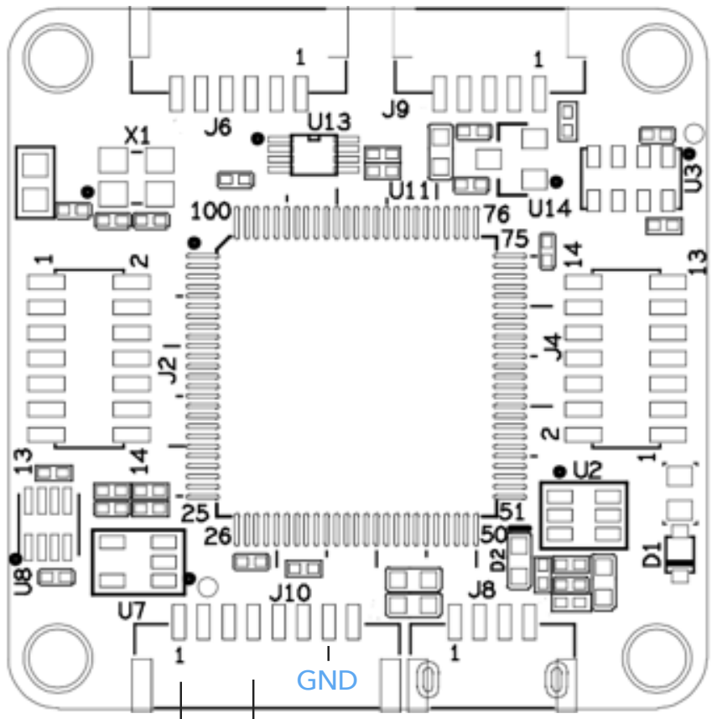
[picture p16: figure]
GND

Fig. 7 on board PWM outputs

When use heatsink mounting, just wire the PWM output pin 1-4 to the corresponding numbered motor/ ESC on the frame (and do not forget to wire GND at any possible).

MRPDB mounting wiring

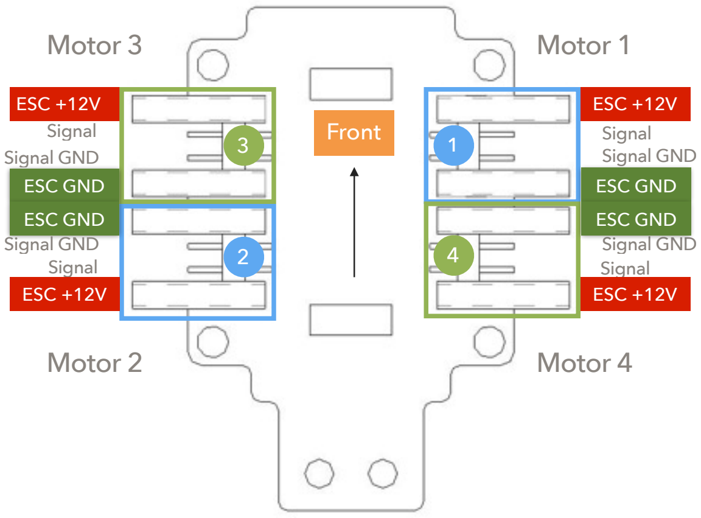
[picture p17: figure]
ESC +12V; Front; Motor 3; Motor 1; Motor 2; Motor 4; ESC GND; Signal Signal GND; Signal; Signal GND; ESC GND ESC GND

Fig. 8 MRPDB pin out map

PWM output pin 1 - 4

Using MRPDB the wiring process is soldering-free. When mounted on MRPDB, the PWM outputs is routed to the MRPDB. The wiring work is as simple as just plug the ESC headers into corresponding numbered motor ports on MRPDB, as illustrated in above picture, and that is all.

### On board Connectors

The MindRacer board provide all necessary interfaces in a racing configuration, including power, RC in, TELEM2, and PWM outputs.

### Remote

MindRacer can support most of the popular remote controller on the market through its one-wire input interface.
For PWM output receiver, please use a PWM-to-PPM encoder to convert the signal and connect to MindRacer’s RC input port.
For most of the PPM/SBUS remote controller, you can directly connect the output of the receiver to MindRacer’s RC input port.
For Spektrum DSM/Satellite series, +3.3V power supply is used. The connection cable between the receiver and MindRacer’s RC input is different.
Before any flight, you need to make sure the remote controller is already paired with the receiver. Please check remote controller/receiver vendor’s product manual on how to pair.

### Calibration

MindRacer needs to be calibrated before it can fly. Use QGroundControl(QGC) to connect MindRacer, and calibrates the flight controller following the instructions in QGC.

### Connect to Ground Station

As a professional flight controller, MindRacer has hundreds of parameters that user can tune. Using QGroundControl software from computer is the best way to carefully adjust these parameters. QGroundControl is a free software that anyone can download and use it on the fly. It can be downloaded from http://www.qgroundcontrol.org. Currently it can support all major PC OS platforms including Windows, MacOS, Linux, etc. Select the right version for your OS.
To connect, launch QGroundControl on your PC (Fig. 7).

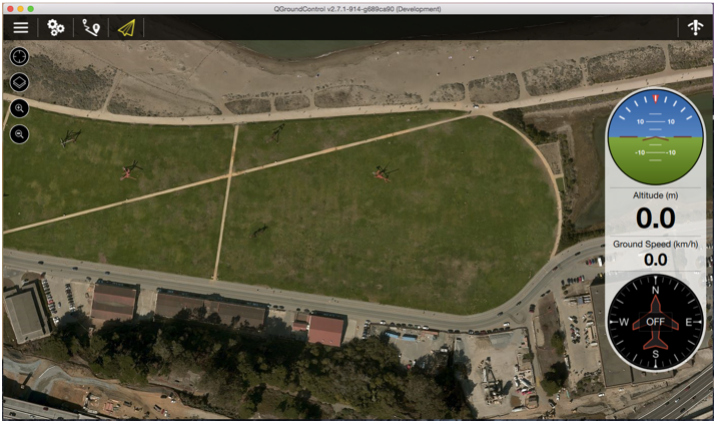
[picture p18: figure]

Fig. 9 Launch QGroundControl
Power OFF the drone first. Use a micro-USB cable to connect the USB port of MindRacer to a PC USB port. The MindRacer flight controller should be powered on. Wait for a few seconds until the flight controllers main LED turns in to any stable color.
For elder version of QGroundControl, click on the ‘Wifi’ icon on the up-right corner, and select the displayed drone name to connect. For version after V2.9.0, QGroundControl can recognize MindRacer and connect automatically.
After connecting is successful, the ground station will update its UI with drone’s status information.

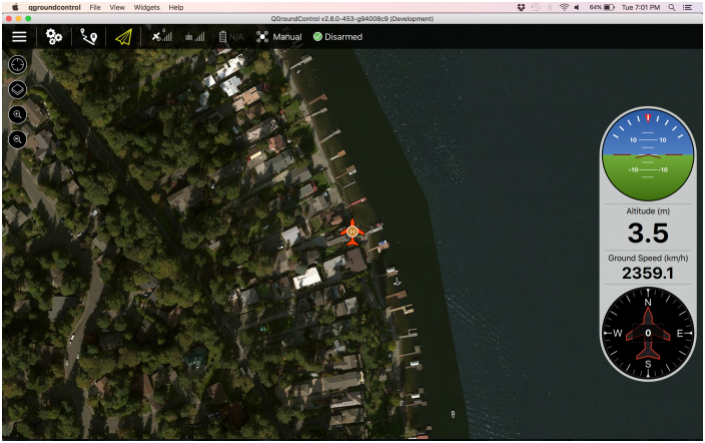
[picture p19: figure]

Fig. 10 drone status information

### Select Flight Mode

Flight modes is pre-set on remote controller as in Fig. By default 4 flight modes are configurable through remote controller: manual, assist/altitude control, assist/position control, and acro mode.
The modes can be chosen by switches in the remote controller (use WFLY/7 7-channel remote controller as an example) as in Fig. 5.

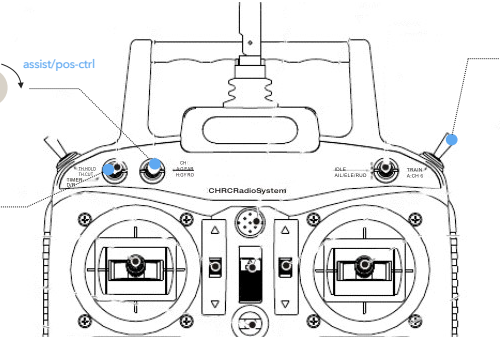
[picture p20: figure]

Fig. 11 remote controller mode switch setting

You can customize and define more flight modes through QGroundControl. Please refer to MindRacer User Guide document for details.

assist/alt-ctrl | assist/pos-ctrl

assist

manual

acro
return-to-land

mission

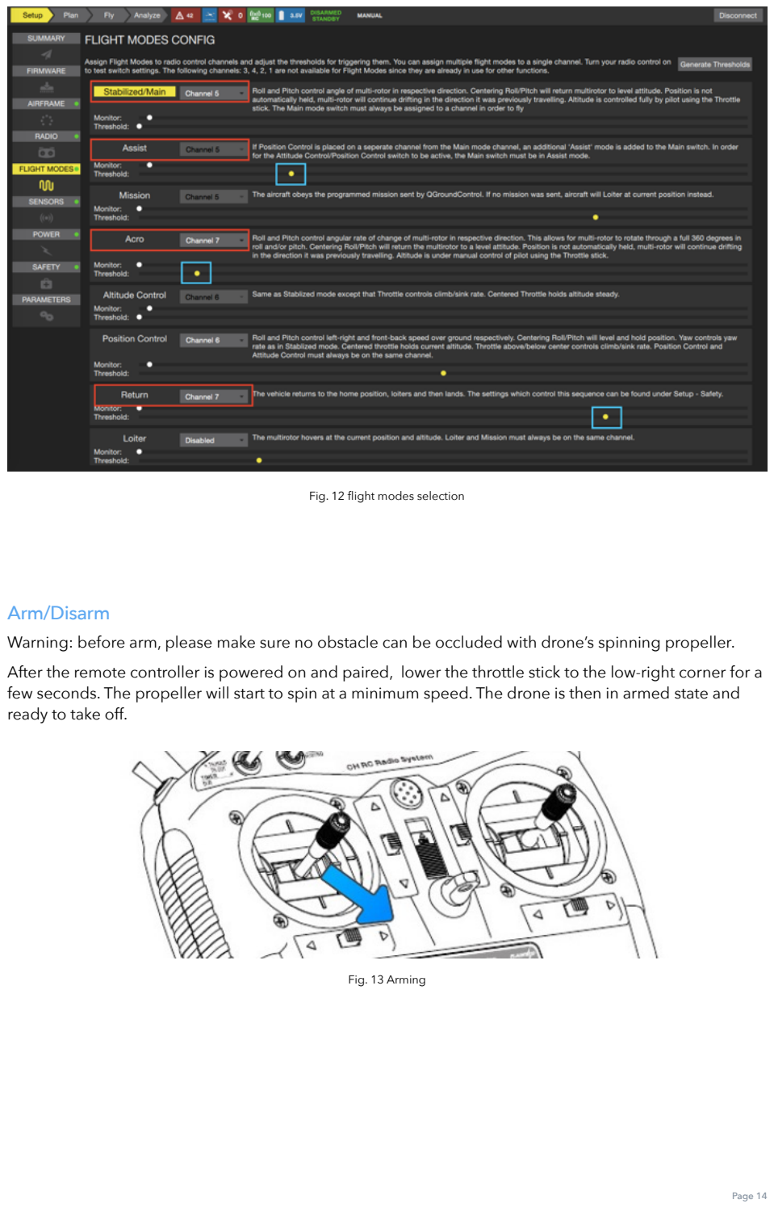
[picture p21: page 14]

Fig. 12 flight modes selection

### Arm/Disarm

Warning: before arm, please make sure no obstacle can be occluded with drone’s spinning propeller. After the remote controller is powered on and paired, lower the throttle stick to the low-right corner for a few seconds. The propeller will start to spin at a minimum speed. The drone is then in armed state and ready to take off.

Fig. 13 Arming

To disarm, lower the throttle stick to the low-left corner for a few seconds, the propellers will stop spinning.

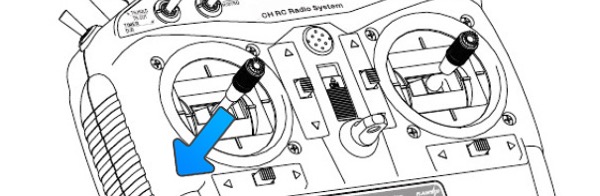
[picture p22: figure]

Fig. 14 Disarming

### Flight Black Box - Using a SD Card

MindRacer has a micro SD (TF) card slot. MindRacer will record flight data into the SD card. It is important for reproducing flight course either for training or maintenance purpose. So it is strongly recommended that user inserting a SD card before take off.
The SD card must be formatted with FAT32.

### OSD

To use an OSD, connect it to MindRacer’s TELEM2 port. You may need to adjust baud rate from QGroundControl depends on the model of OSD you are using.

### The interface breakout board

When using MindRacer in situation other than racing, you may need the breakout board to access other interfaces provided by MindRacer through the pin headers. The breakout board leads out almost all ports available of the processor including GPS, CAN, I2C, UART, etc.

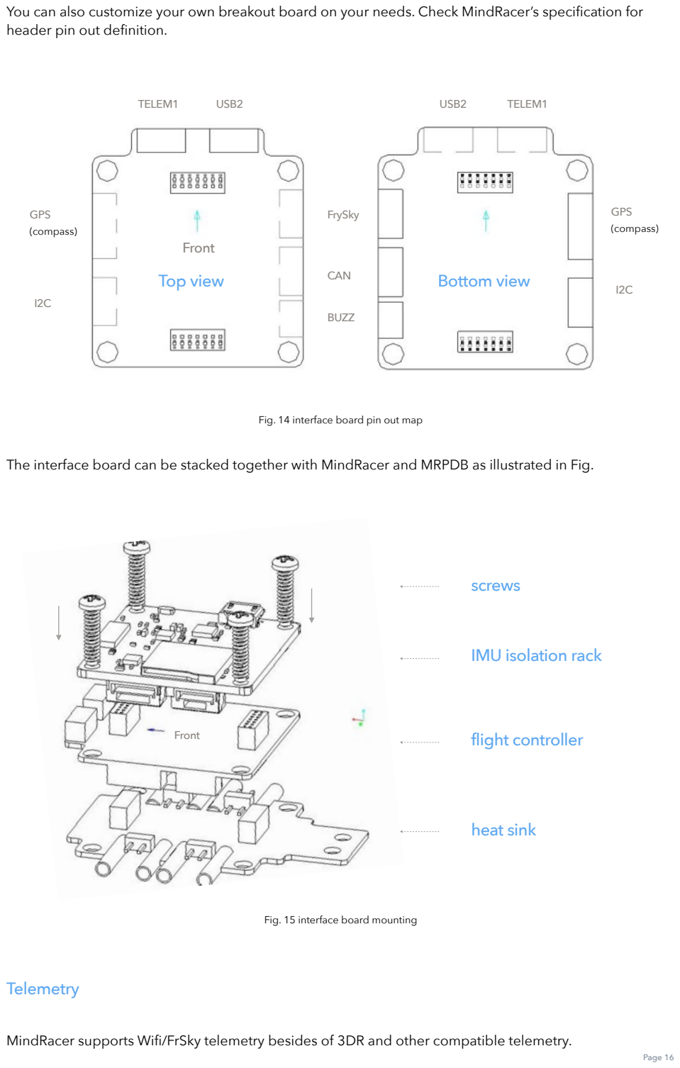
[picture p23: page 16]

You can also customize your own breakout board on your needs. Check MindRacer’s specification for header pin out definition.

Fig. 14 interface board pin out map

The interface board can be stacked together with MindRacer and MRPDB as illustrated in Fig.

Fig. 15 interface board mounting

### Telemetry

MindRacer supports Wifi/FrSky telemetry besides of 3DR and other compatible telemetry.

Front

TELEM1 USB2

GPS
(compass)

I2C

Top view | Bottom view

FrySky

CAN

BUZZ

GPS
(compass)

I2C

USB2 TELEM1

### heat sink

### flight controller

### screws

### IMU isolation rack

Front

3DR and its compatible telemetry
3DR and other compatible telemetry can be connected to either onboard TELEM2 port, or the UART1 port on breakout board.

Wifi telemetry
Wifi telemetry module can be connected to MindRacer board’s TELEM2 port, or UART1 on breakout board.

FrSky telemetry (Smart Port)
FrSky telemetry can be connected to UART4/FrSky port on breakout board.

### Connect a GPS

MindRacer can also use an external GPS to locate its global position. Connect GPS module’s connector to MindRacer’s ‘GPS’ socket on breakout board.
Check the signal strength before take off using a GPS. When connect to QGroundControl you can see the GPS signal strength indicator on screen. More bars mean better signal. The GPS can only work well when there are at least 3 bars.
In order to use external compass instead of internal compass, you need to re-calibrate the compass sensor in QGroundControl.

### Color LED Indicator

The main LED indicator is a tricolor LED and can show different status information with the combination of different colors and blinks. The status information it indicates is listed below:

Fig. 16 LED indicator

LED color | meaning (status) | remark
Solid any color | Armed
Breathing any color | Standby
Amber | Low battery or Failsafe | (Return to home, etc)
Blue | GPS not locked
Green | GPS Locked
Fast Blink & Red | Arming error
Blink & Red | Other error
Transitional Green | Mode switch success

### Support

Please visit www.mindpx.org for more information. Or you can send email to support@mindpx.net for any inquiries or help.

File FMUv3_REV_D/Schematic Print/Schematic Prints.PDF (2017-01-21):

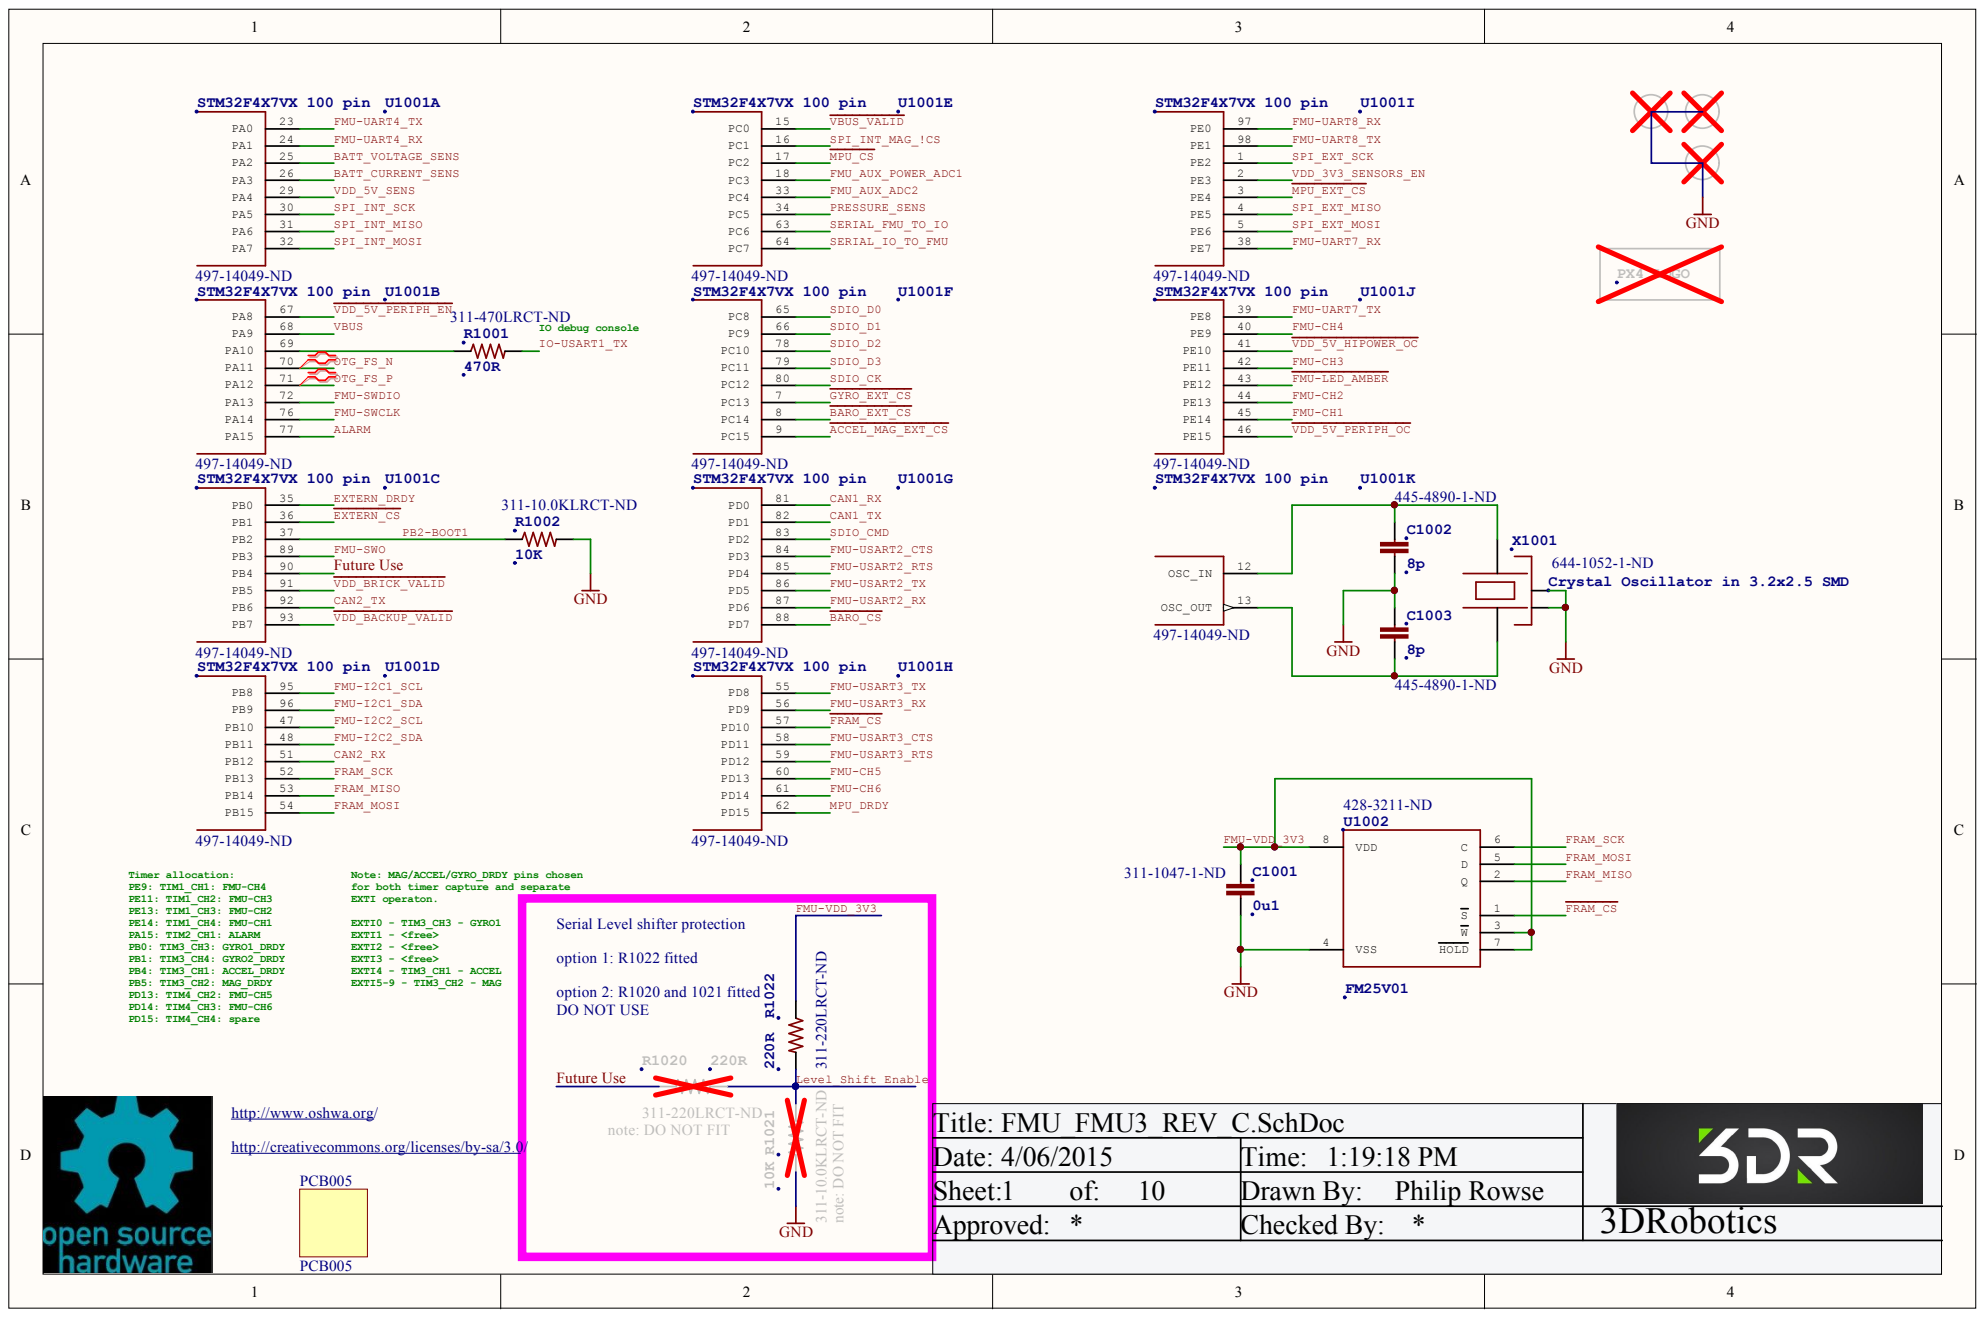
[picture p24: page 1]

Note: MAG/ACCEL/GYRO_DRDY pins chosen
for both timer capture and separate
EXTI operaton.

Serial Level shifter protection

http://www.oshwa.org/

311-220LRCT-ND
note: DO NOT FIT

Title: FMU_FMU3_REV_C.SchDoc
Date: 4/06/2015 | Time: 1:19:18 PM
Sheet:1 of: 10 | Drawn By: Philip Rowse
Approved: * | Checked By: * | 3DRobotics

http://creativecommons.org/licenses/by-sa/3.0/

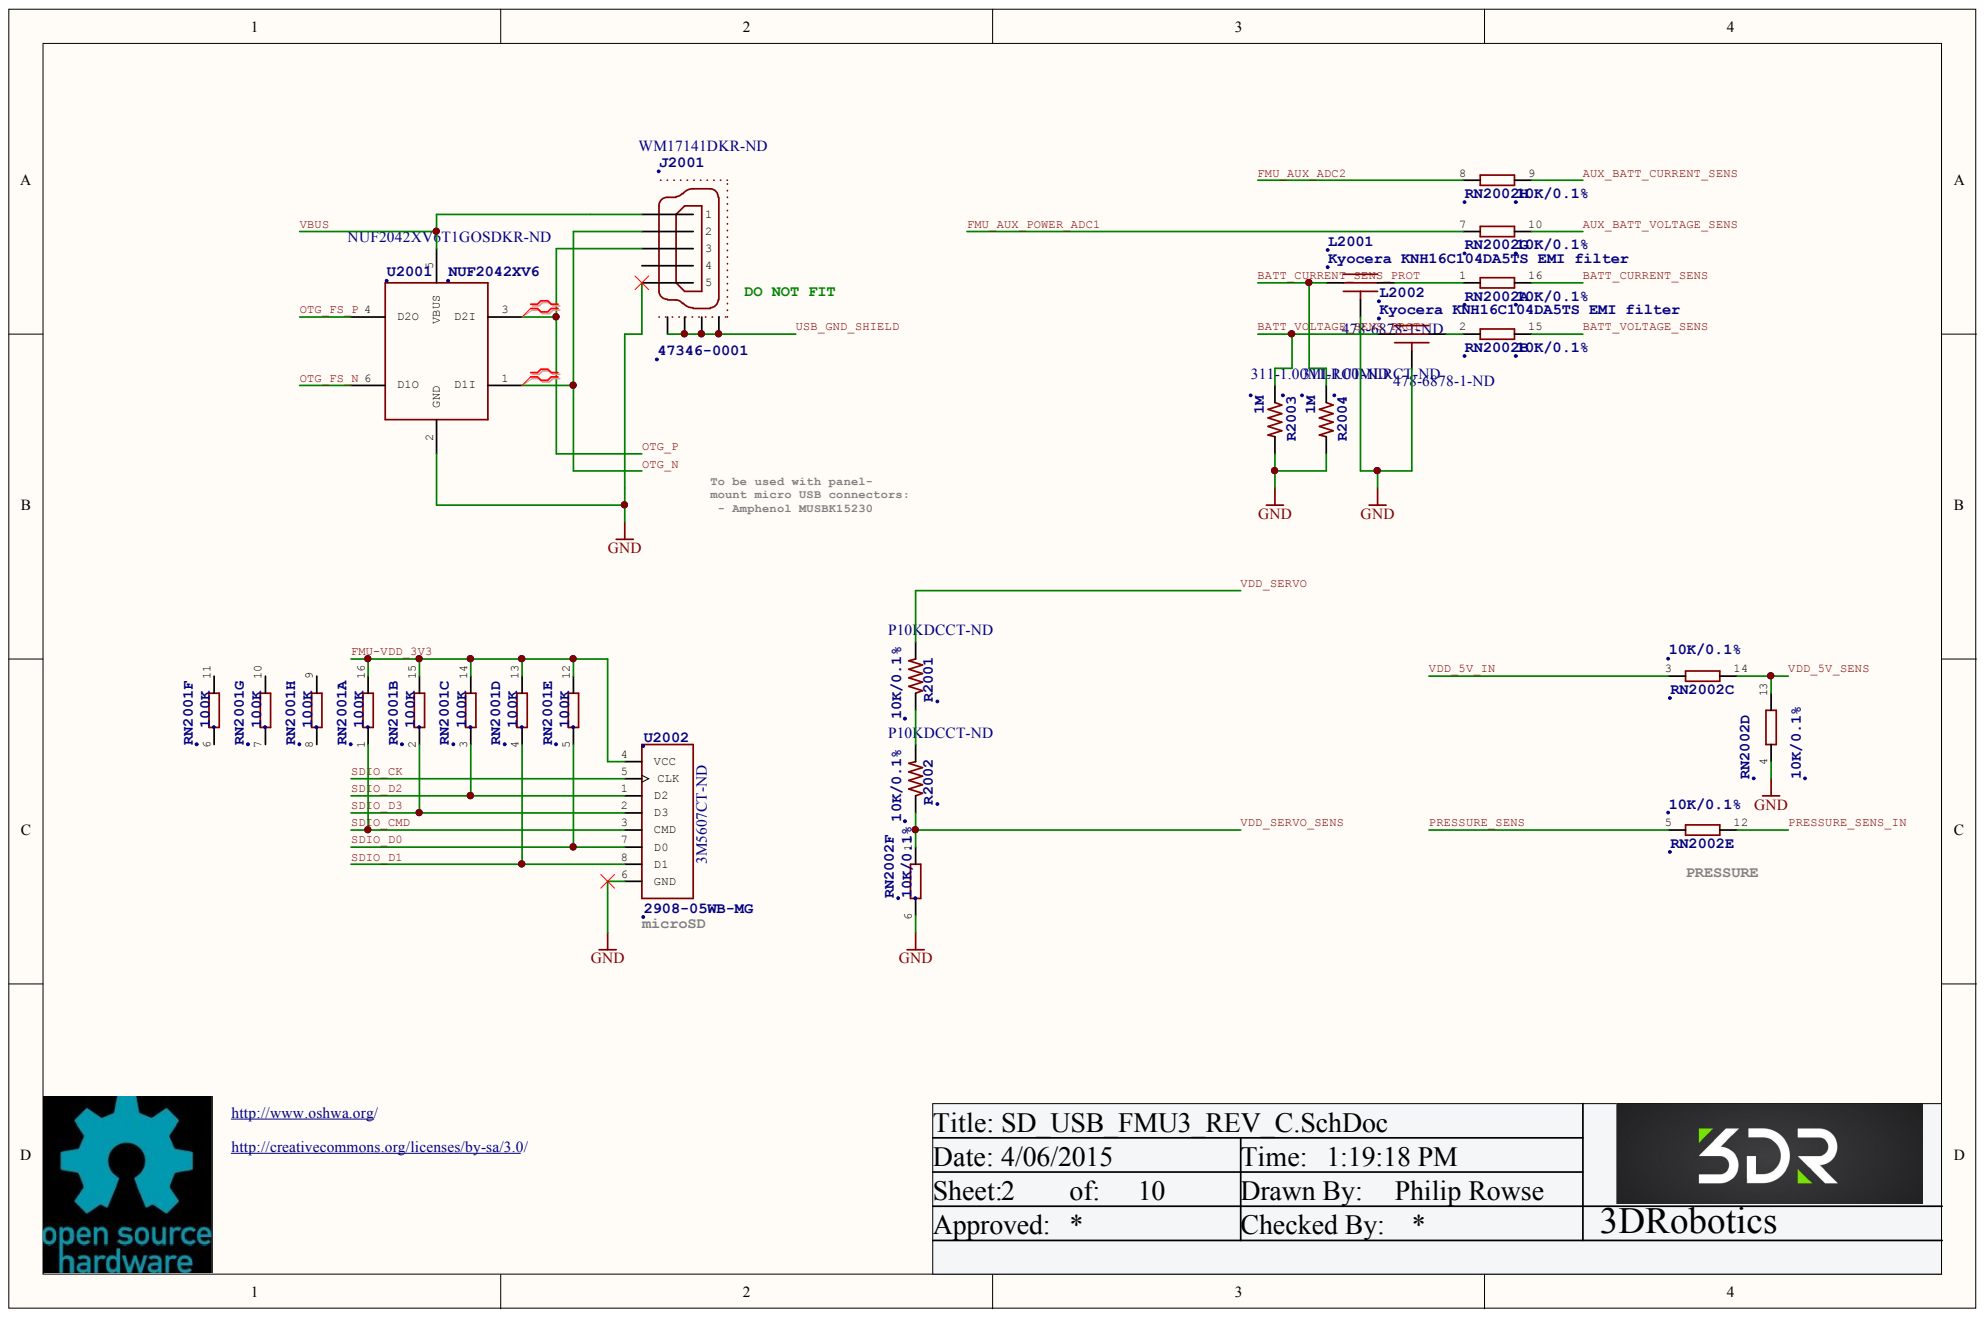
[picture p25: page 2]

Kyocera KNH16C104DA5TS EMI filter 478-6878-1-ND

Title: SD_USB_FMU3 _REV_C.SchDo c
Date: 4/0 6/2 0 1 5 | Time: 1:1 9:1 8 PM
Sheet: 2 of: 1 0 | Drawn By : Philip Rowse
Ap pro ved : * | Checked By : * | 3DRobotics

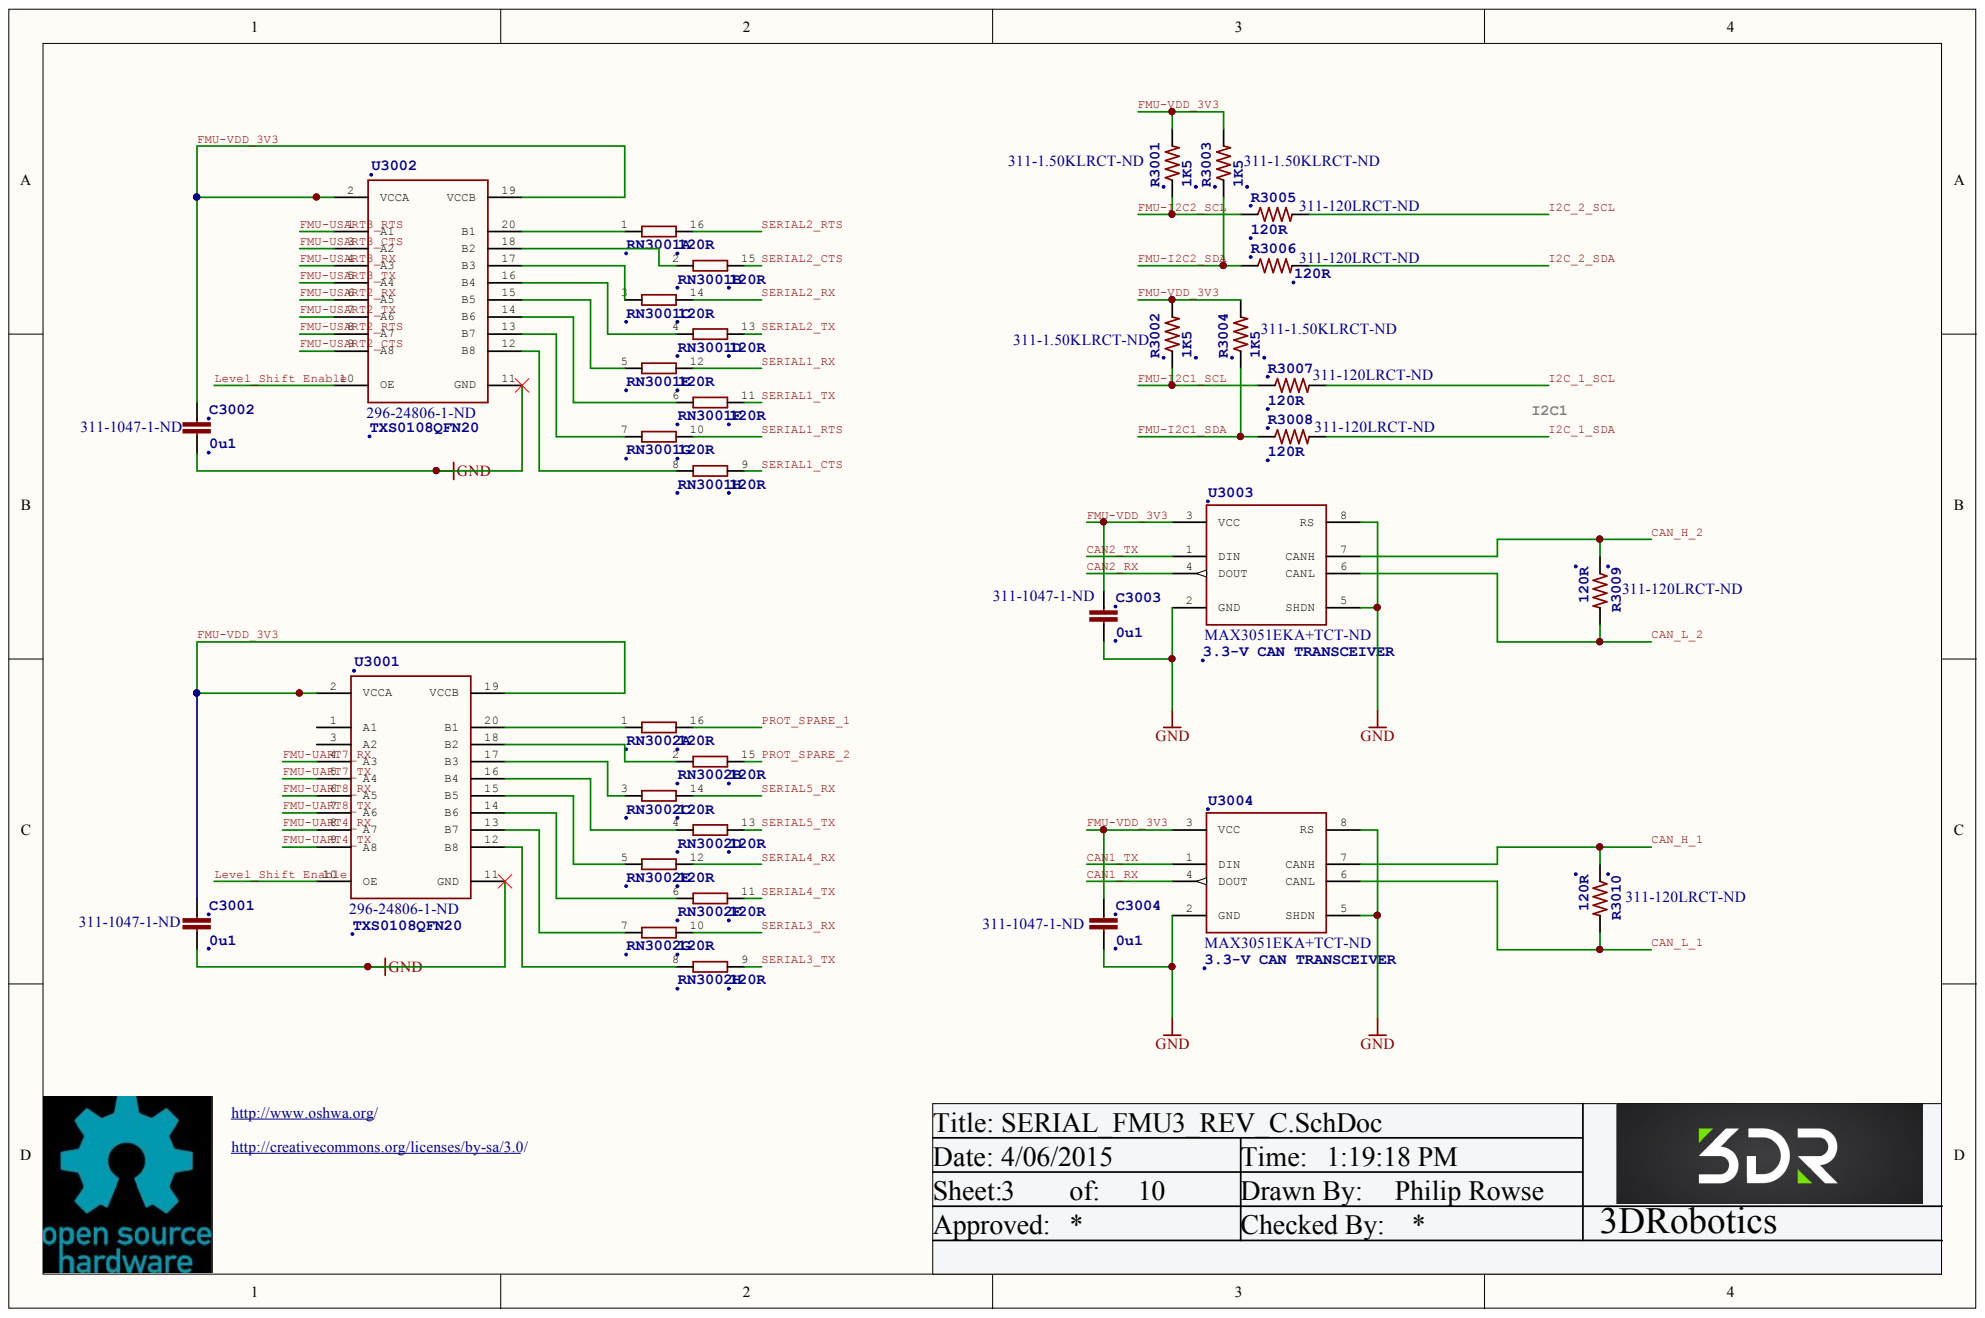
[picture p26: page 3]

Title: SERIAL_FMU3 _REV_C.SchDo c
Date: 4/0 6/2 0 1 5 | Time: 1:1 9:1 8 PM
Sheet: 3 of: 1 0 | Drawn By : Philip Rowse
Ap pro ved : * | Checked By : * | 3DRobotics

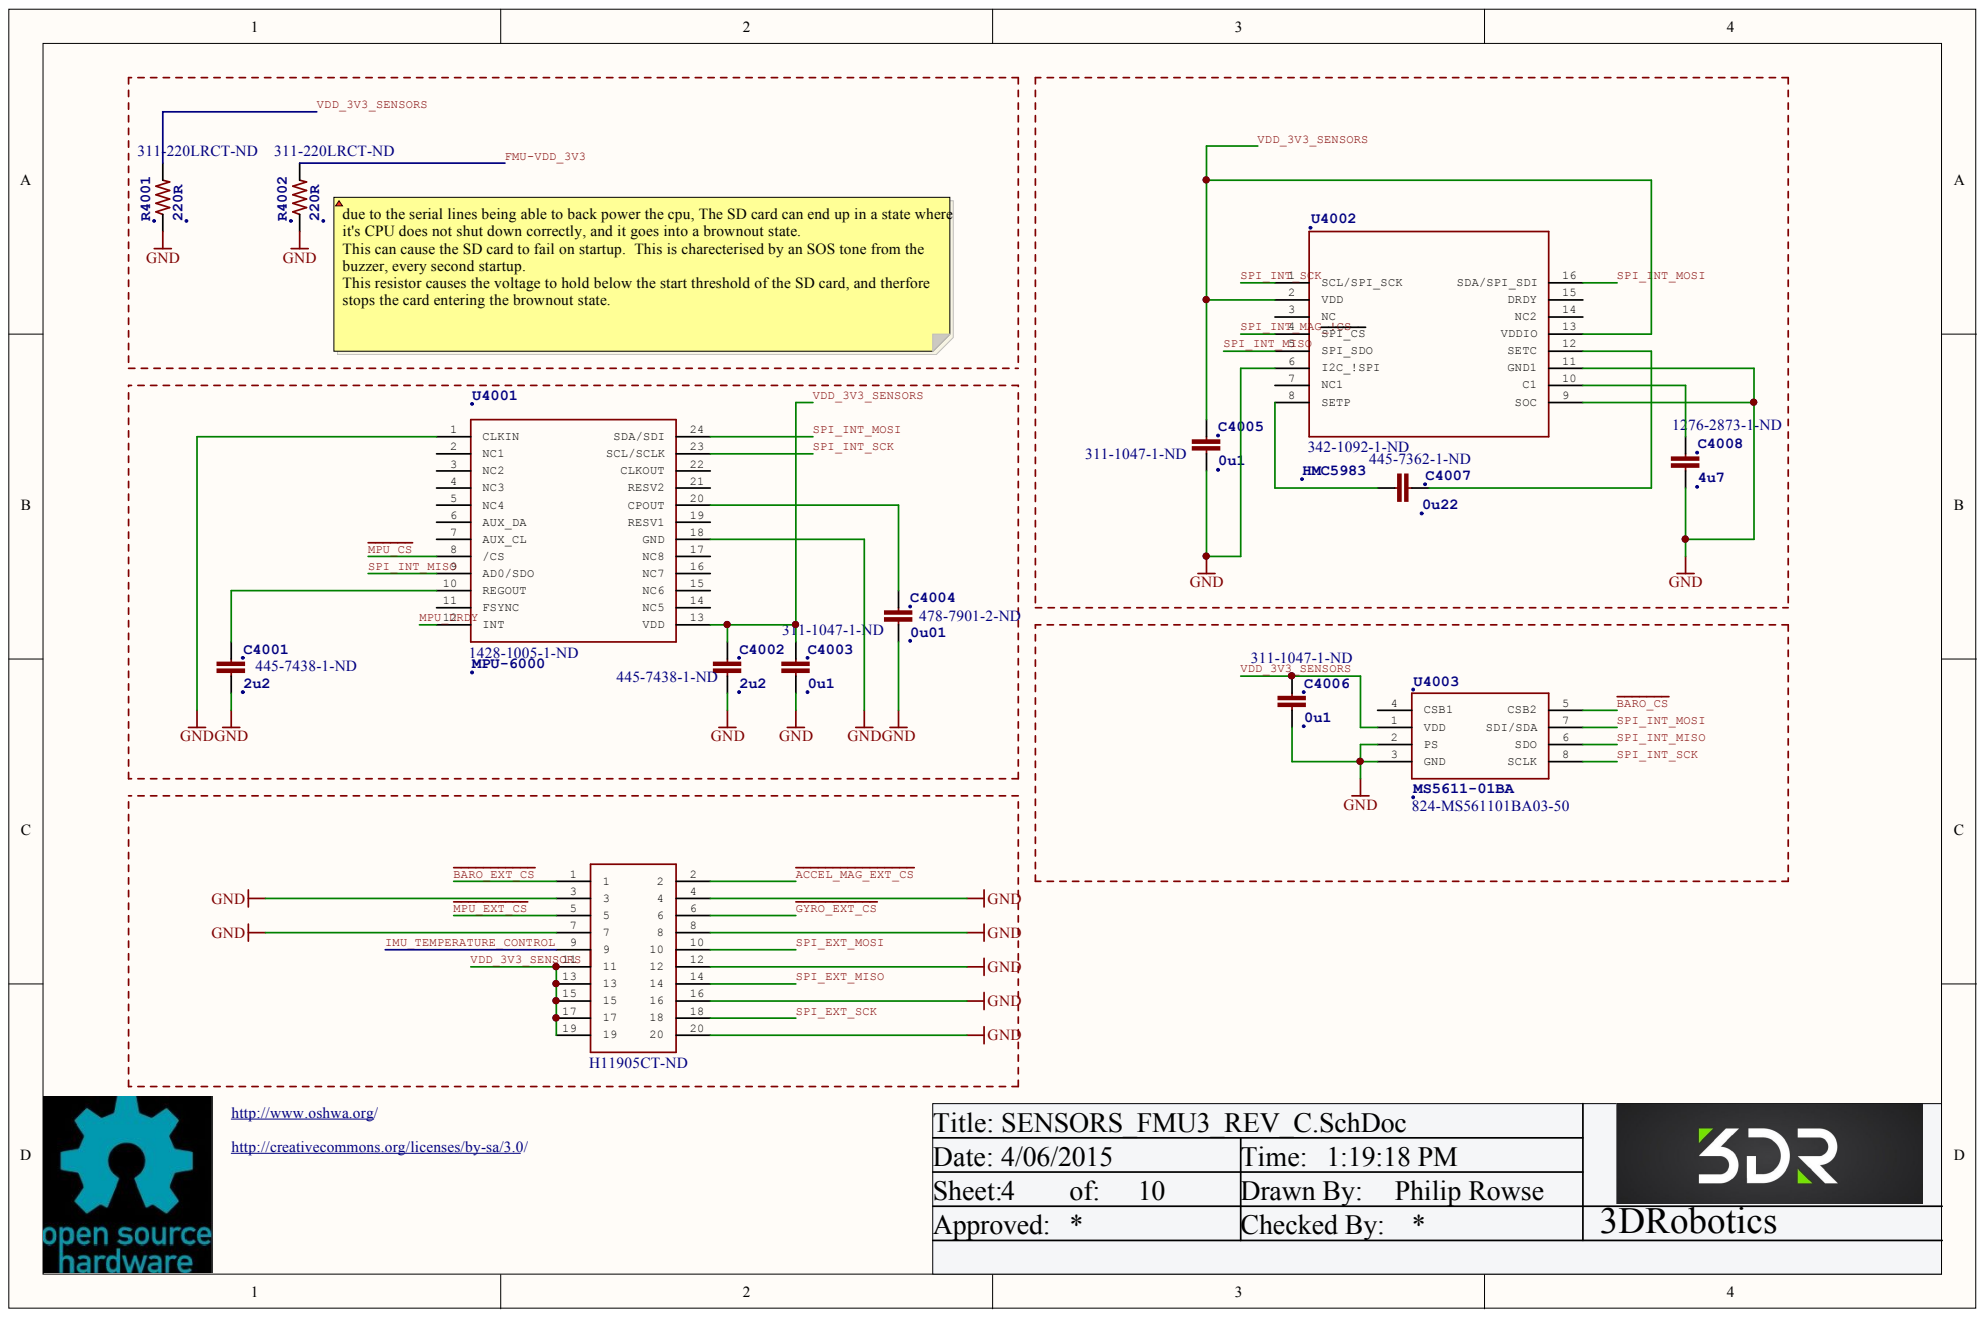
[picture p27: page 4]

he SD card, an

Title: SENSORS_FMU3 _REV_C.SchDo c
Date: 4/0 6/2 0 1 5 | Time: 1:1 9:1 8 PM
Sheet: 4 of: 1 0 | Drawn By : Philip Rowse
Ap pro ved : * | Checked By : * | 3DRobotics

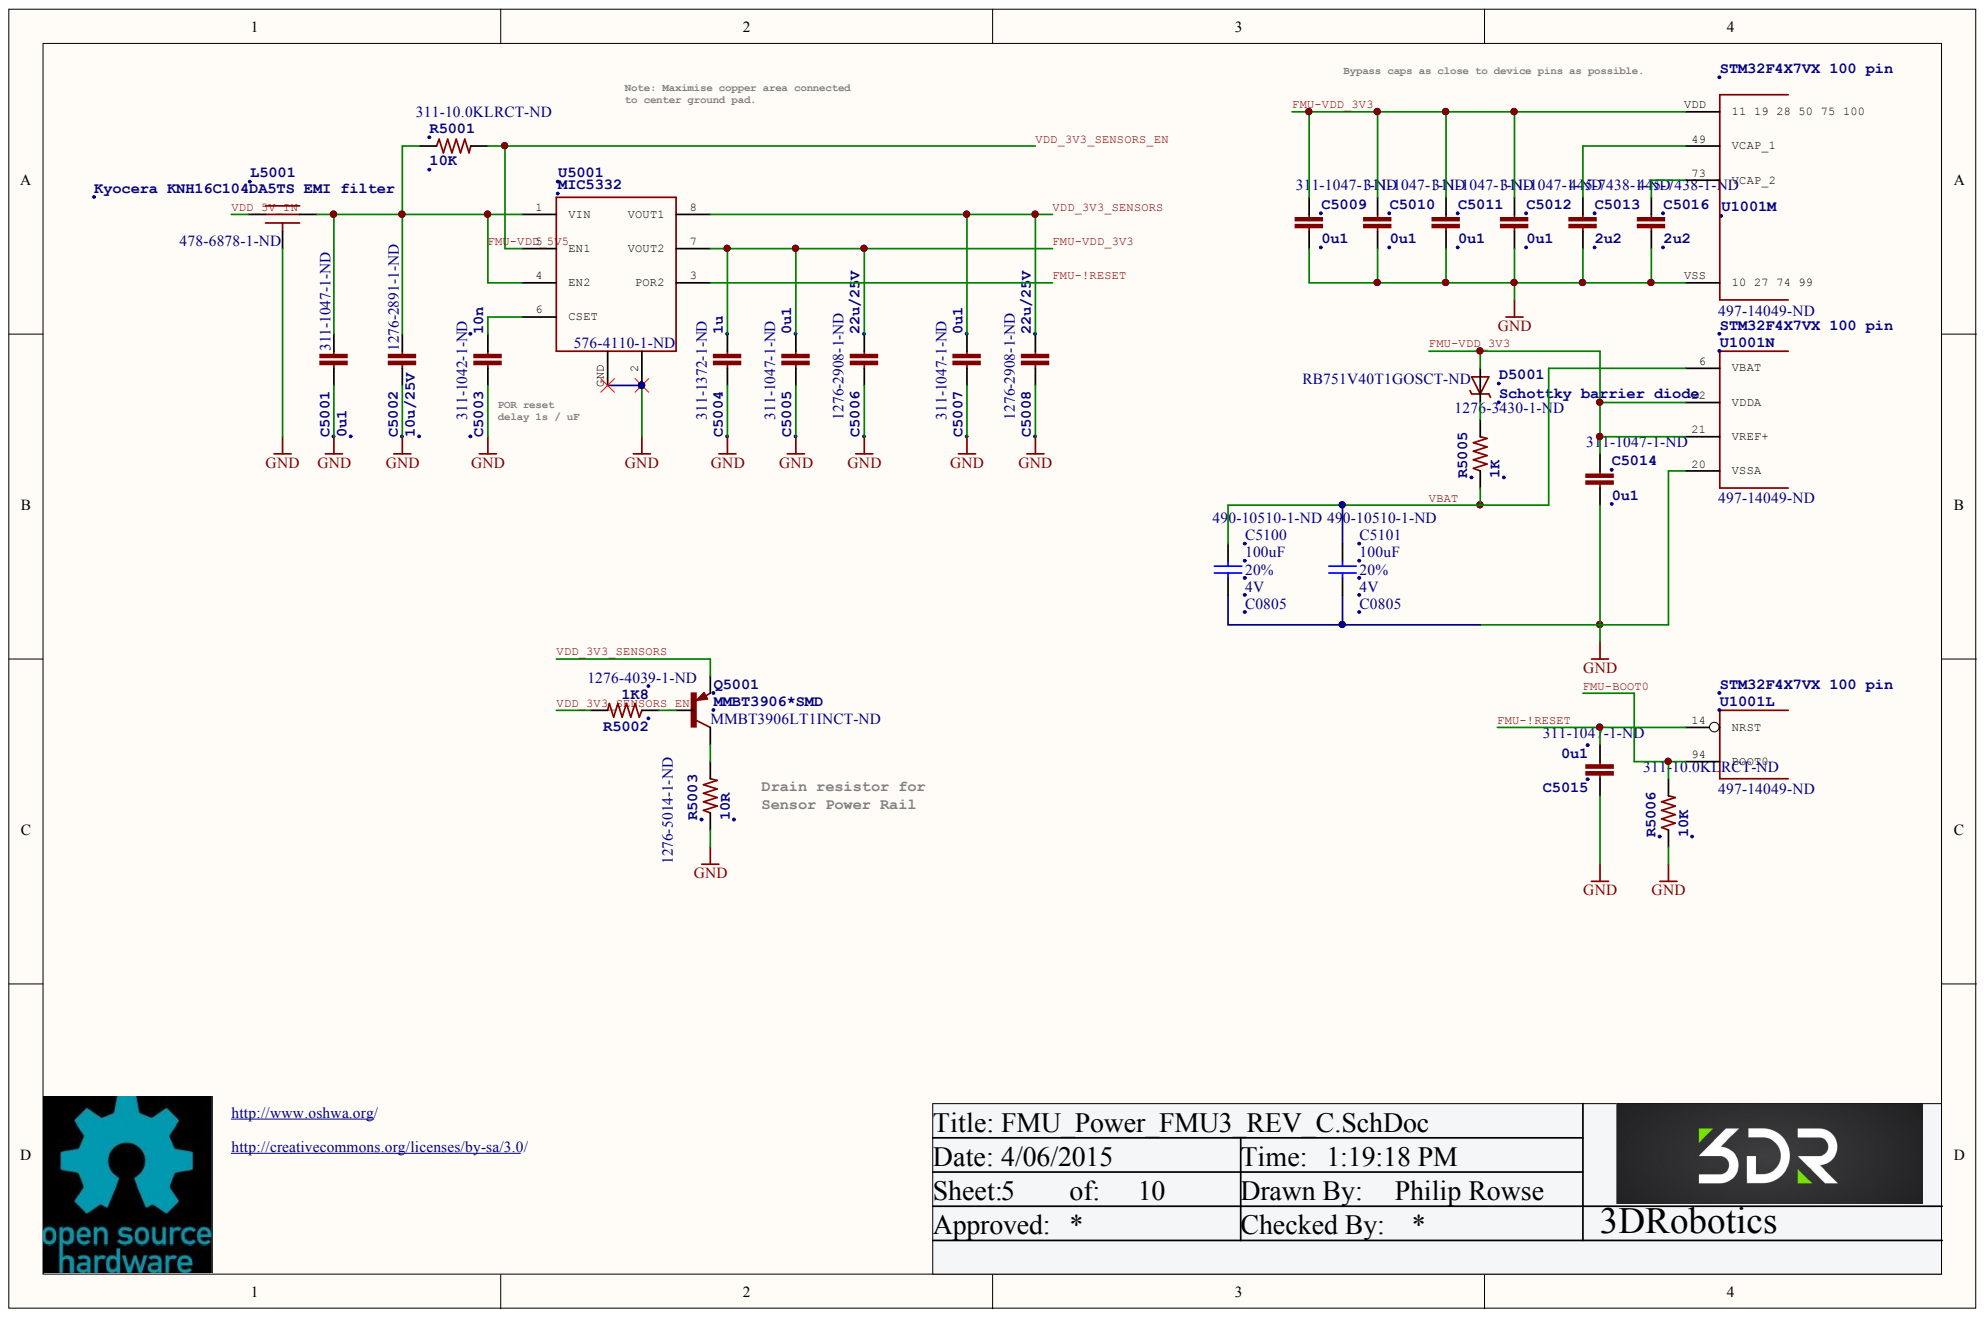
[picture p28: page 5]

Title: FMU_Power_FMU3 _REV_C.SchDo c
Date: 4/0 6/2 0 1 5 | Time: 1:1 9:1 8 PM
Sheet: 5 of: 1 0 | Drawn By : Philip Rowse
Ap pro ved : * | Checked By : * | 3DRobotics

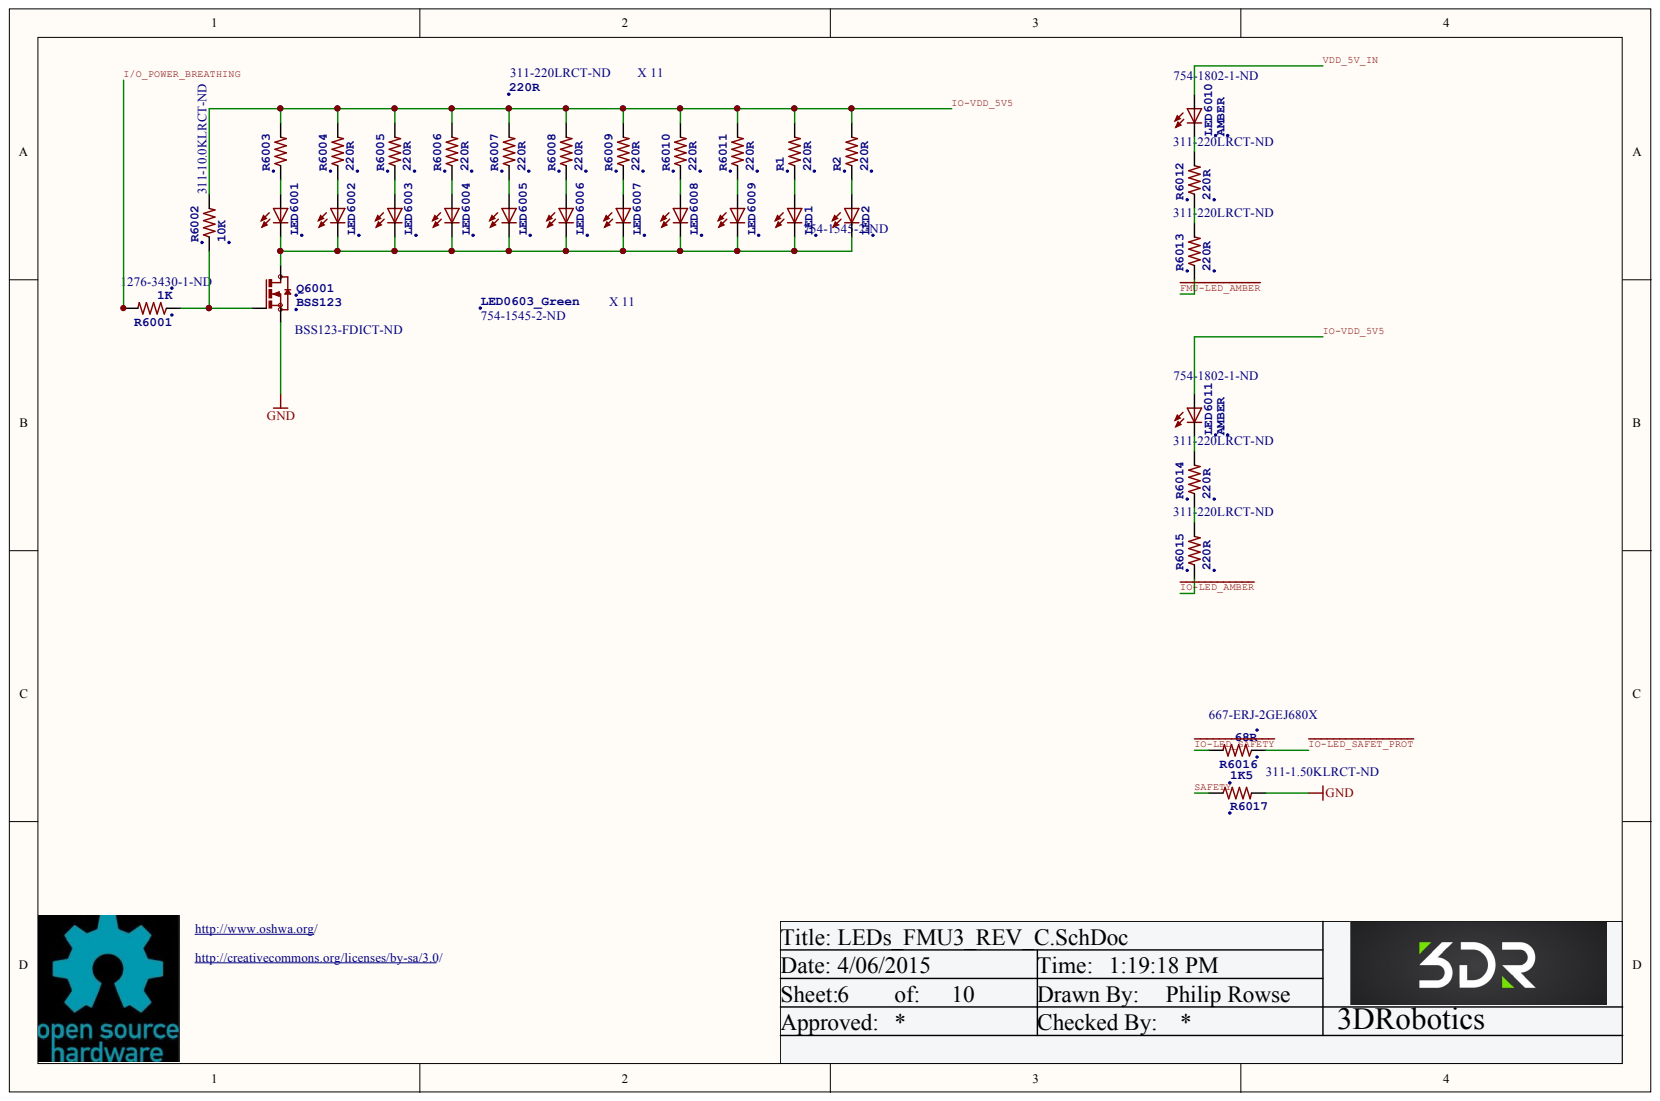
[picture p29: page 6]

Title: LEDs_FMU3 _REV_C.SchDo c
Date: 4/0 6/2 0 1 5 | Time: 1:1 9:1 8 PM
Sheet: 6 of: 1 0 | Drawn By : Philip Rowse
Ap pro ved : * | Checked By : * | 3DRobotics

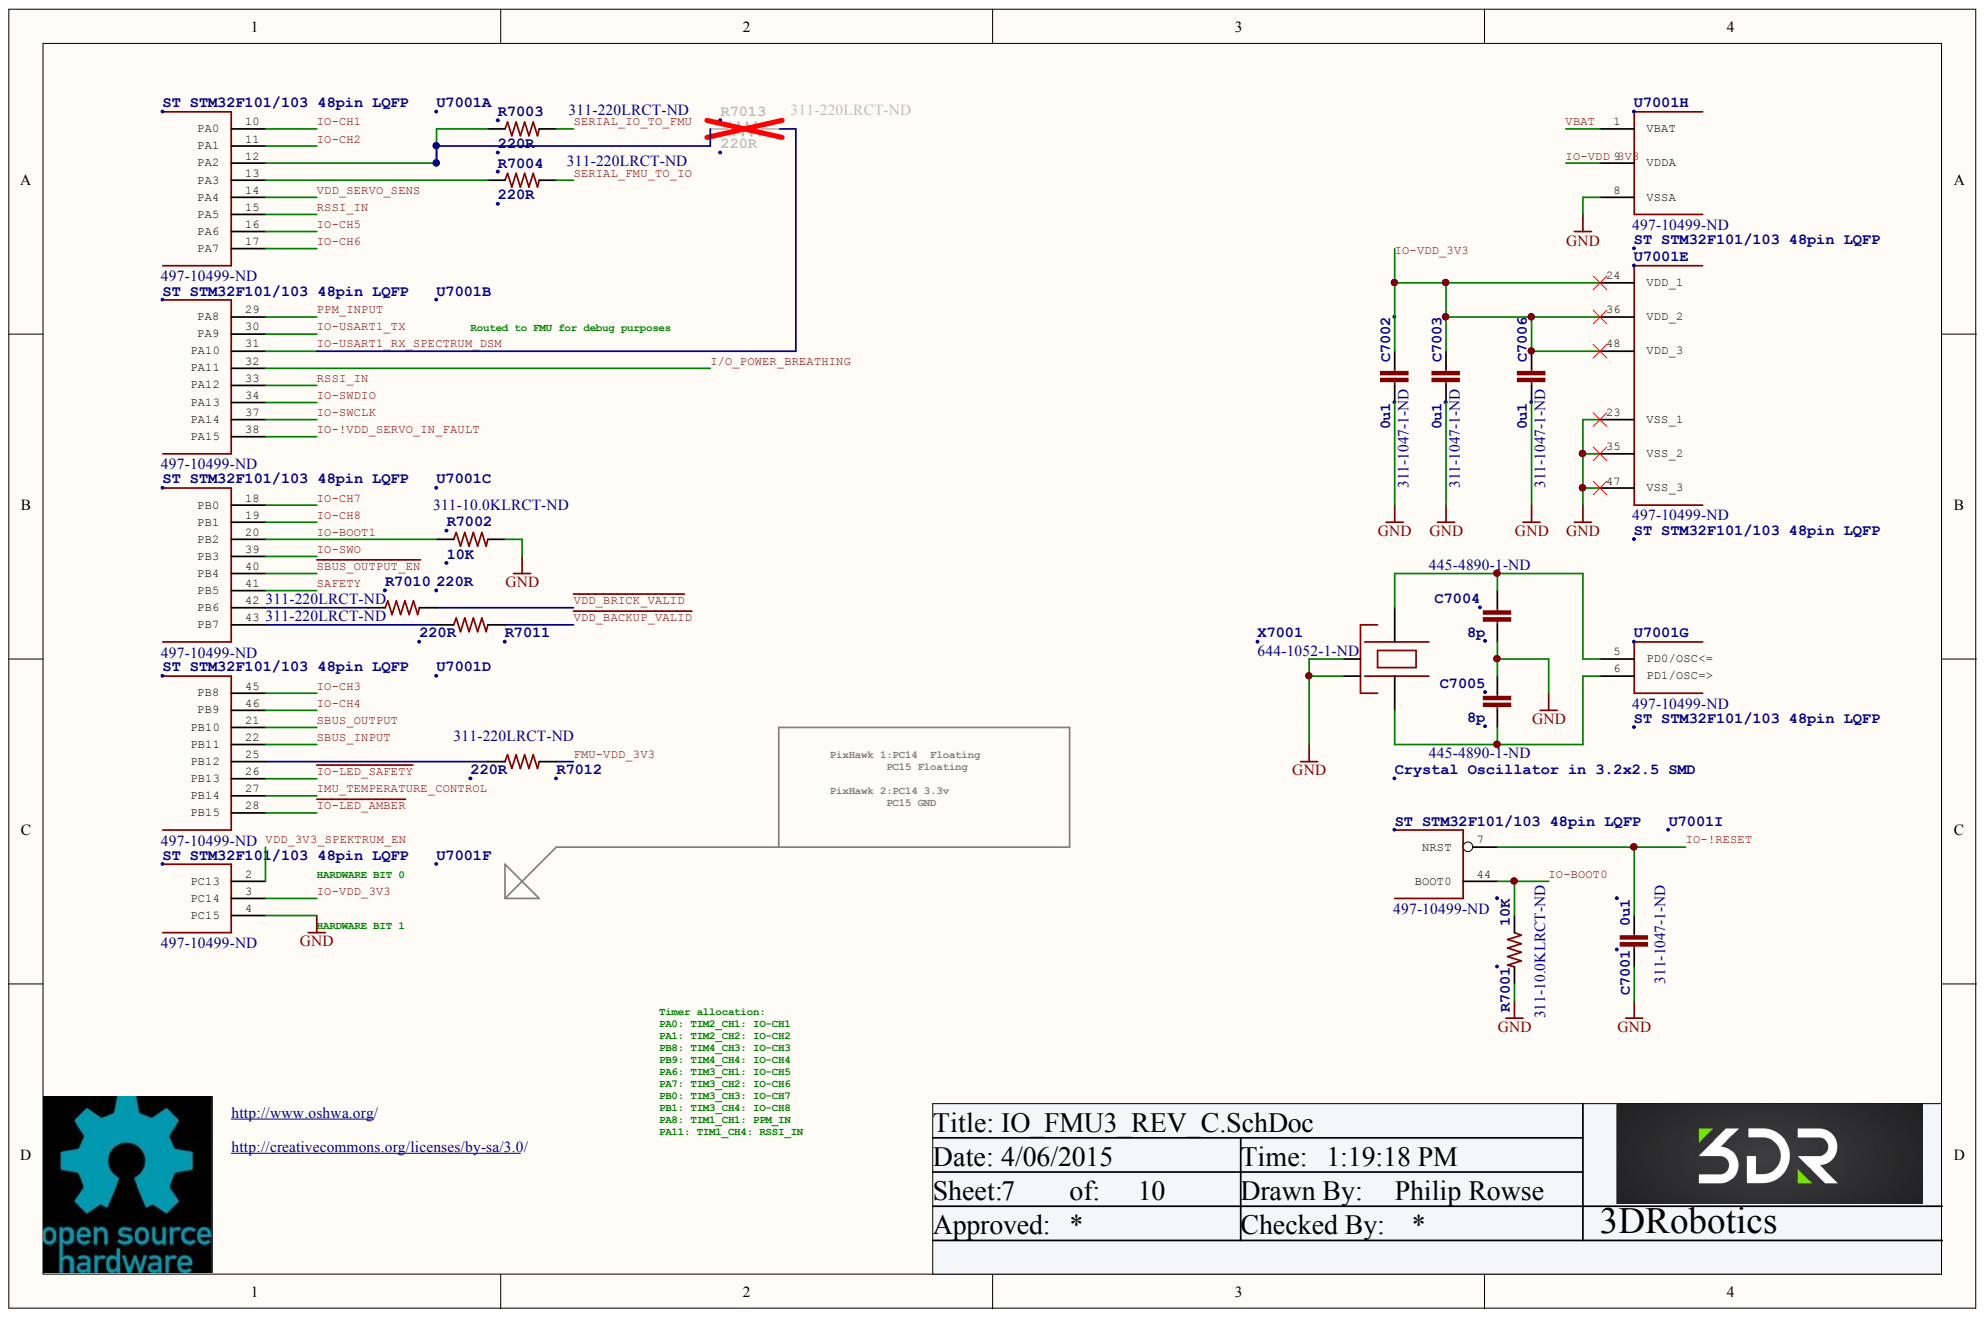
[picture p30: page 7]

1 1 | I O -C H 2 | 220R
1 2

Crystal Oscillator in 3.2x2.5 SMD 311-1047-1-ND C7006 0u1 311-1047-1-ND C7003 0u1 311-1047-1-ND

Title: IO_FMU3 _REV_C.SchDo c
Date: 4/0 6/2 0 1 5 | Time: 1:1 9:1 8 PM
Sheet: 7 of: 1 0 | Drawn By : Philip Rowse
Ap pro ved : * | Checked By : * | 3DRobotics

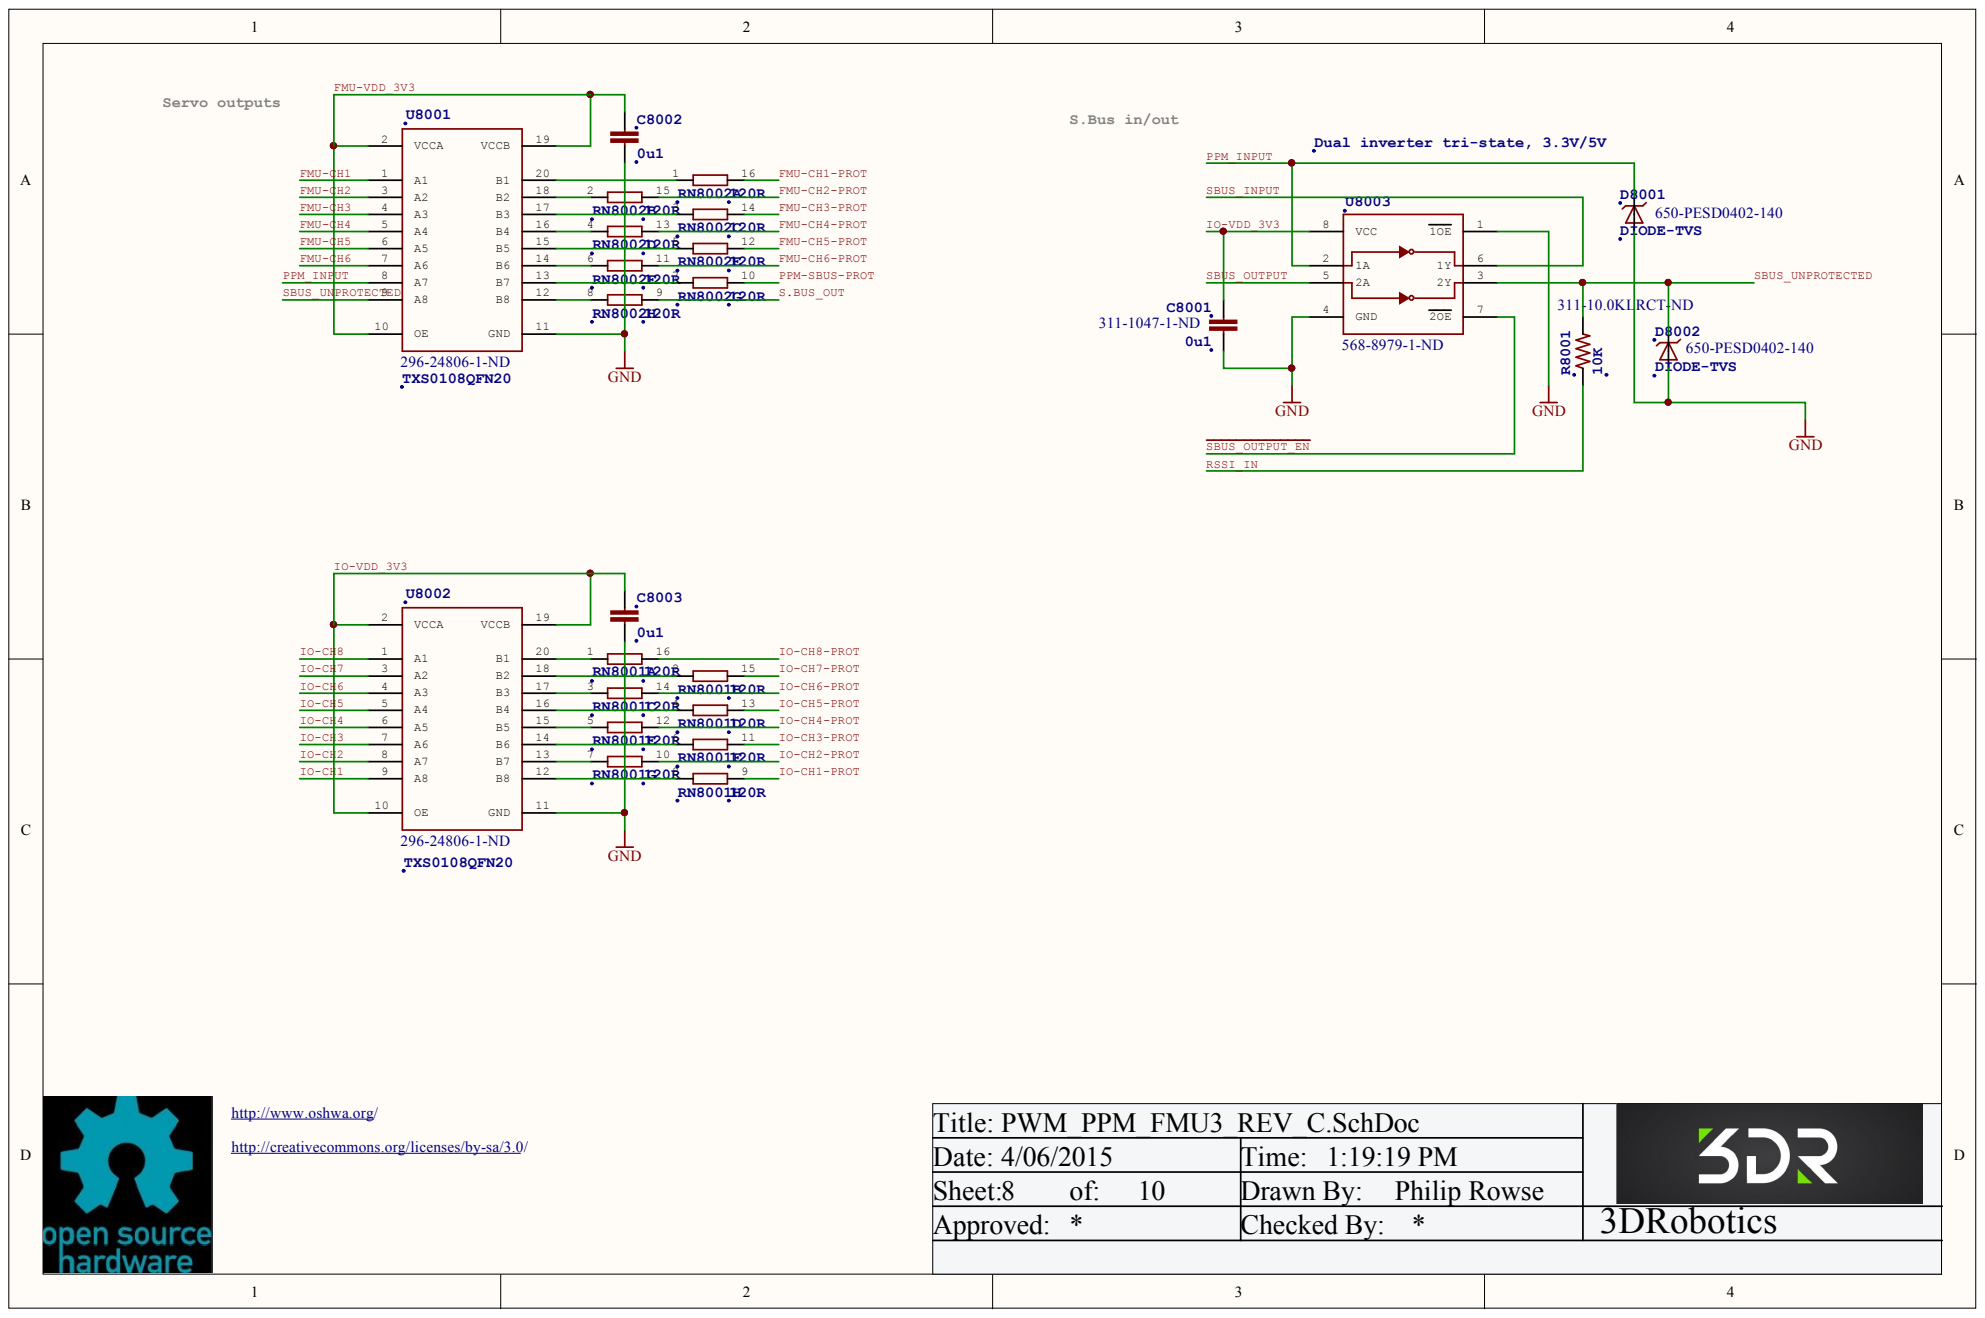
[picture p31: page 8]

Dual inverter tri-state, 3.3V/5V 311-10.0

Title: PWM _PPM _FMU3 _REV_C.SchDo c
Date: 4/0 6/2 0 1 5 | Time: 1:1 9:1 9 PM
Sheet: 8 of: 1 0 | Drawn By : Philip Rowse
Ap pro ved : * | Checked By : * | 3DRobotics

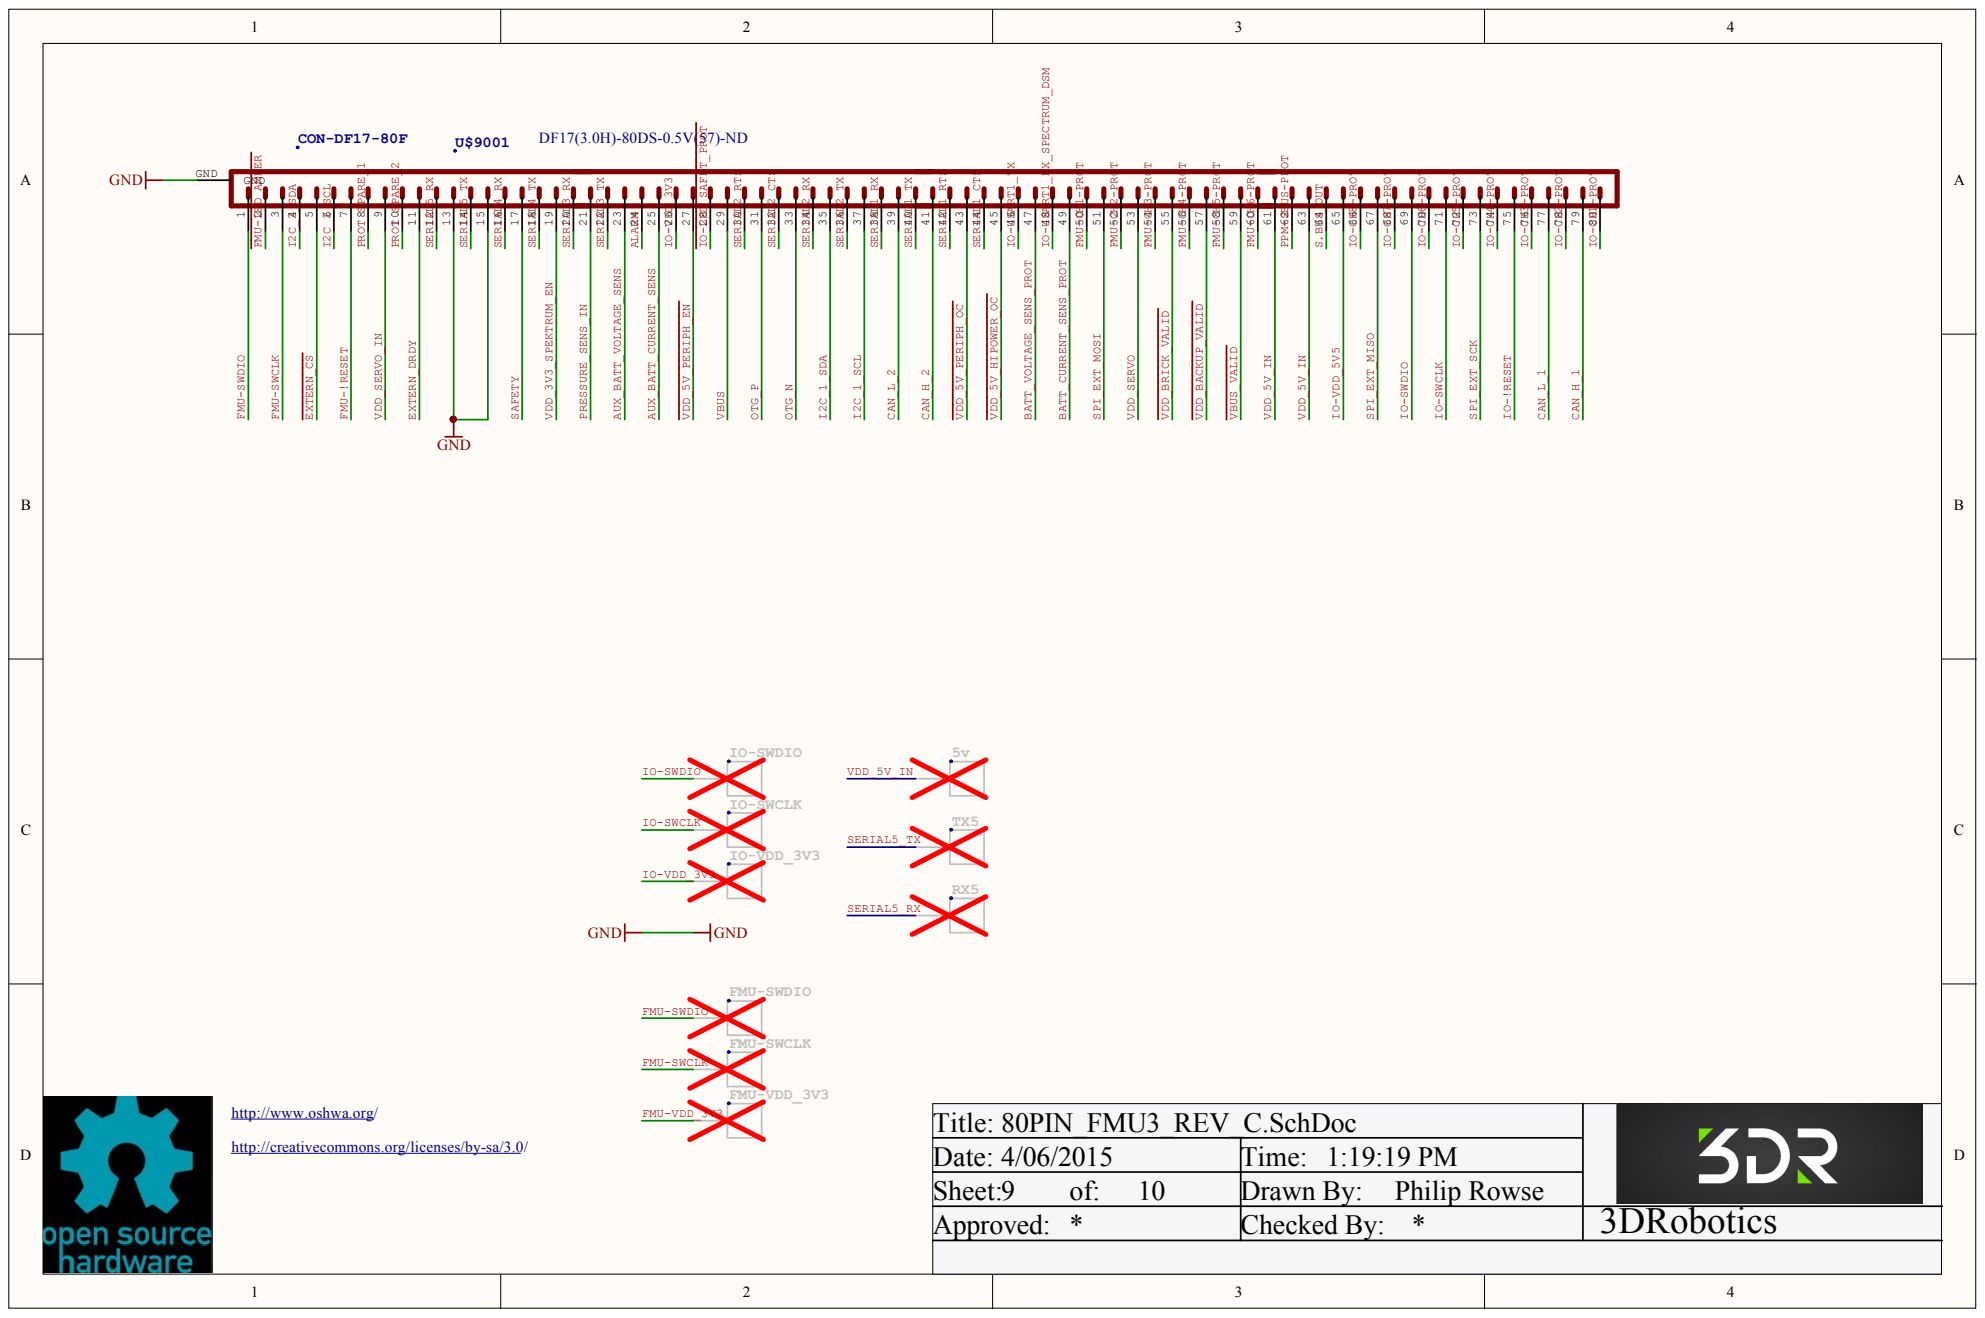
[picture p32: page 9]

http://www.oshwa.org/

Title: 80PIN_FMU3_REV_C.SchDoc
Date: 4/06/2015 | Time: 1:19:19 PM
Sheet:9 of: 10 | Drawn By: Philip Rowse
Approved: * | Checked By: * | 3DRobotics

http://creativecommons.org/licenses/by-sa/3.0/

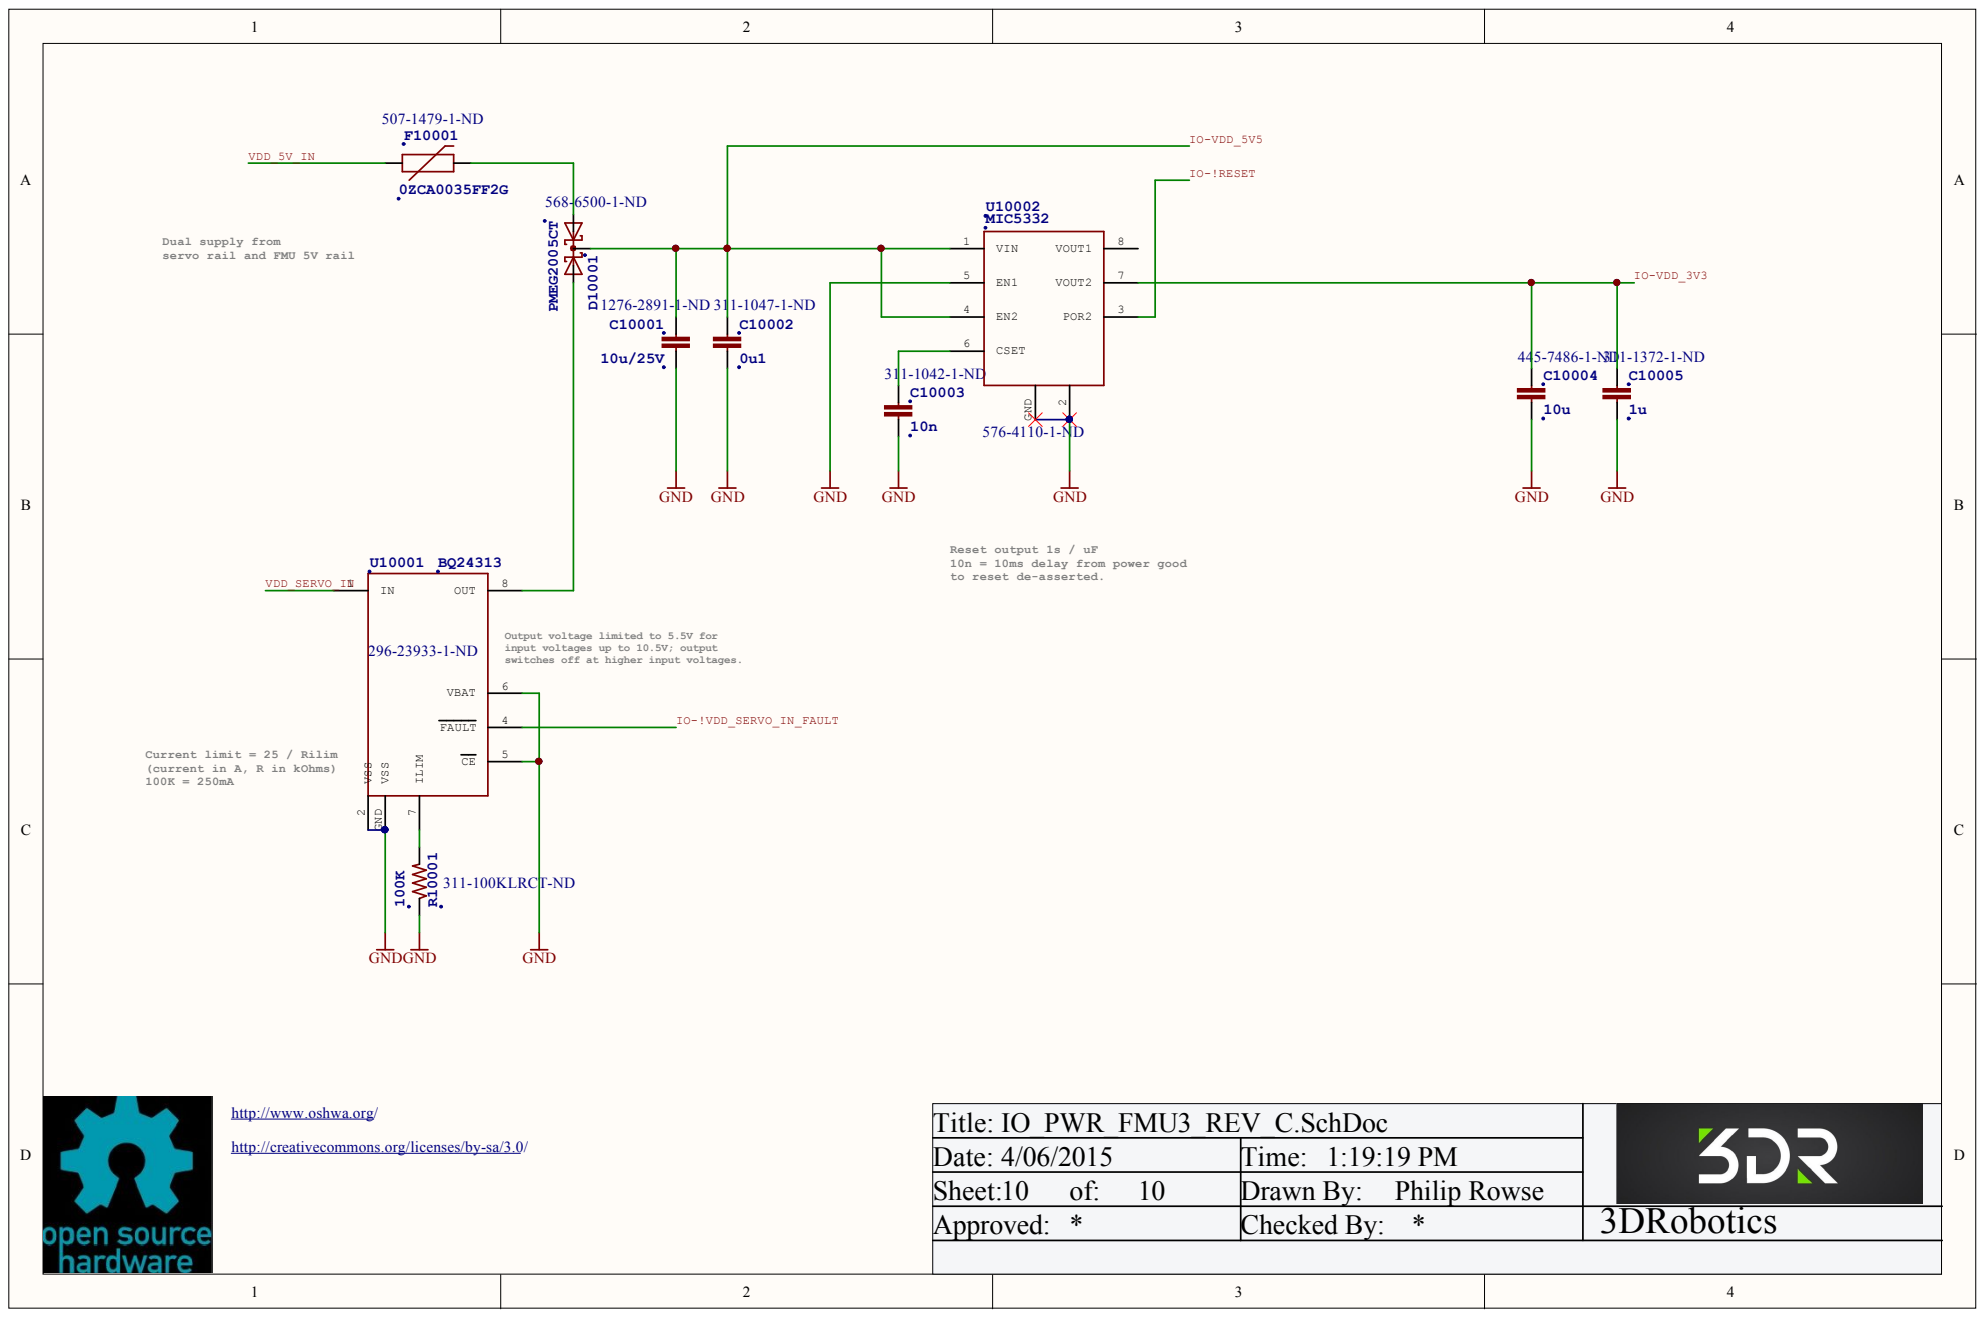
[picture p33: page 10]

Dual supply from
servo rail and FMU 5V rail

Reset output 1s / uF
10n = 10ms delay from power good
to reset de-asserted.

Output voltage limited to 5.5V for
input voltages up to 10.5V; output
switches off at higher input voltages.

Current limit = 25 / Rilim
(current in A, R in kOhms)

http://www.oshwa.org/

Title: IO_PWR_FMU3_REV_C.SchDoc
Date: 4/06/2015 | Time: 1:19:19 PM
Sheet:10 of: 10 | Drawn By: Philip Rowse
Approved: * | Checked By: * | 3DRobotics

http://creativecommons.org/licenses/by-sa/3.0/

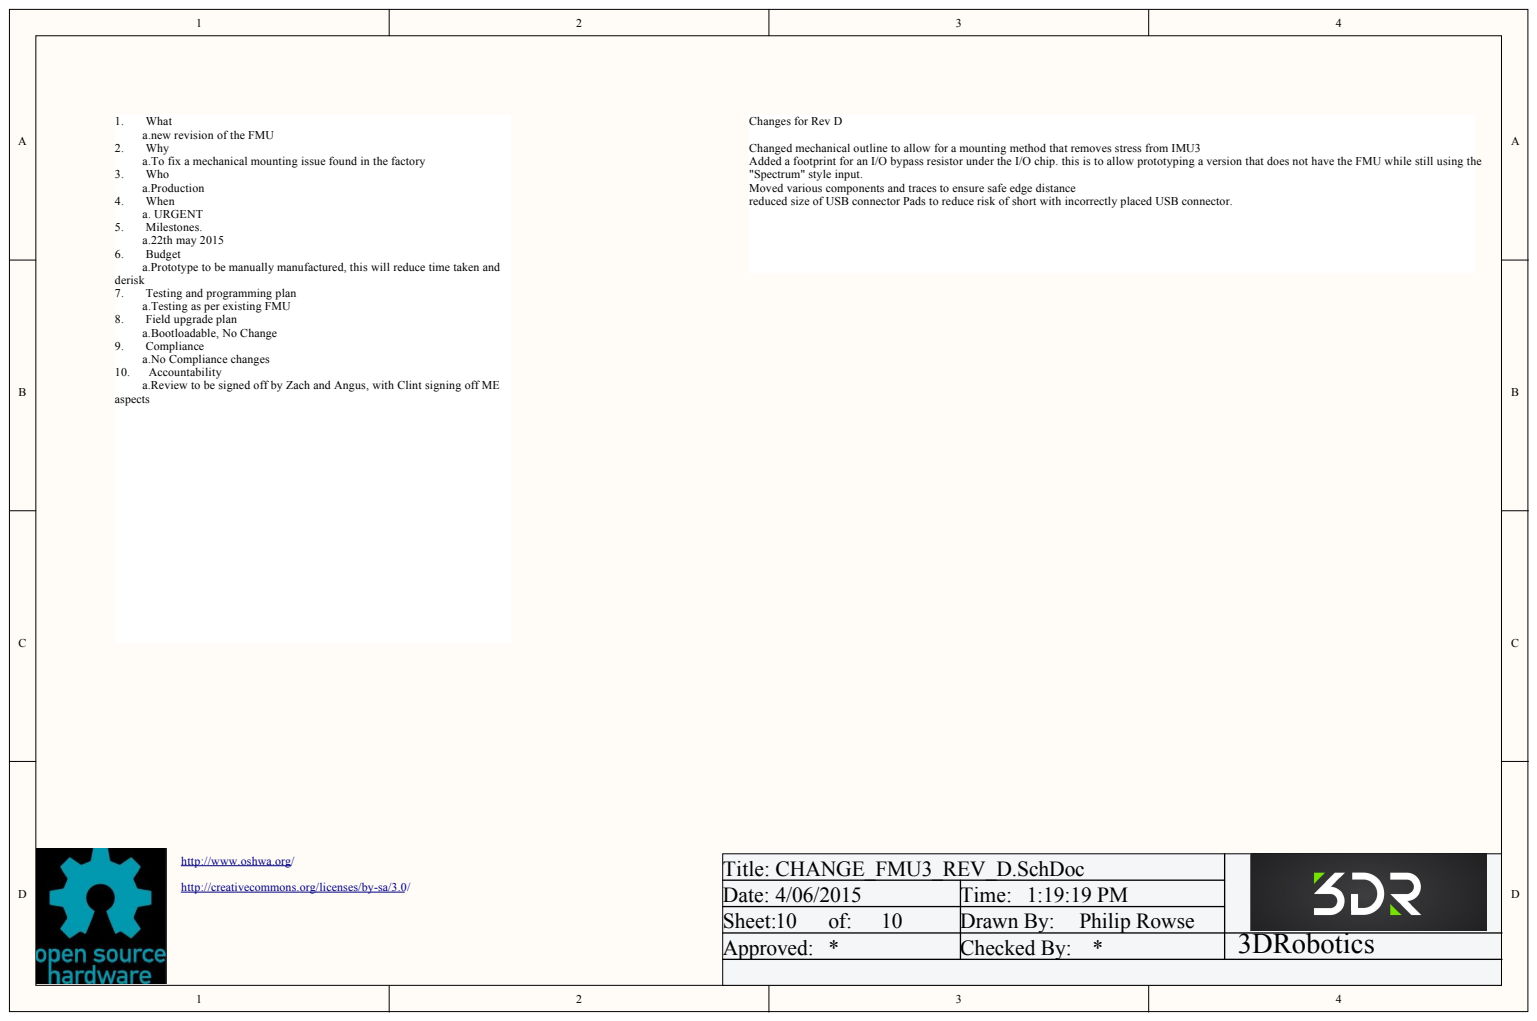
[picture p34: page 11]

1. What
a.new revision of the FMU
2. Why
a.To fix a mechanical mounting issue found in the factory
3. Who
a.Production
4. When
a. URGENT
5. Milestones.
a.22th may 2015
6. Budget
a.Prototype to be manually manufactured, this will reduce time taken and
derisk
7. Testing and programming plan
a.Testing as per existing FMU
8. Field upgrade plan
a.Bootloadable, No Change
9. Compliance
a.No Compliance changes
10. Accountability
a.Review to be signed off by Zach and Angus, with Clint signing off ME
aspects

Changed mechanical outline to allow for a mounting method that removes stress from IMU3
Added a footprint for an I/O bypass resistor under the I/O chip. this is to allow prototyping a version that does not have the FMU while still using the
"Spectrum" style input.
Moved various components and traces to ensure safe edge distance
reduced size of USB connector Pads to reduce risk of short with incorrectly placed USB connector.

http://www.oshwa.org/

Title: CHANGE_FMU3_REV_D.SchDoc
Date: 4/06/2015 | Time: 1:19:19 PM
Sheet:10 of: 10 | Drawn By: Philip Rowse
Approved: * | Checked By: * | 3DRobotics

http://creativecommons.org/licenses/by-sa/3.0/

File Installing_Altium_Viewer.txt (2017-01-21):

go to http://www.altium.com/altium-designer-viewer
Register for your Free license.

With this license you can use most features of altium within this file, ie, cross probing, viewing etc...

To edit, you will need a licenced version of Altium.

As the FMU is 8 layers, it cannot be made in the free version of Eagle... but I would be happy if someone 
could help with the conversion to any other file formats.

Please contact me by raising an issue here.

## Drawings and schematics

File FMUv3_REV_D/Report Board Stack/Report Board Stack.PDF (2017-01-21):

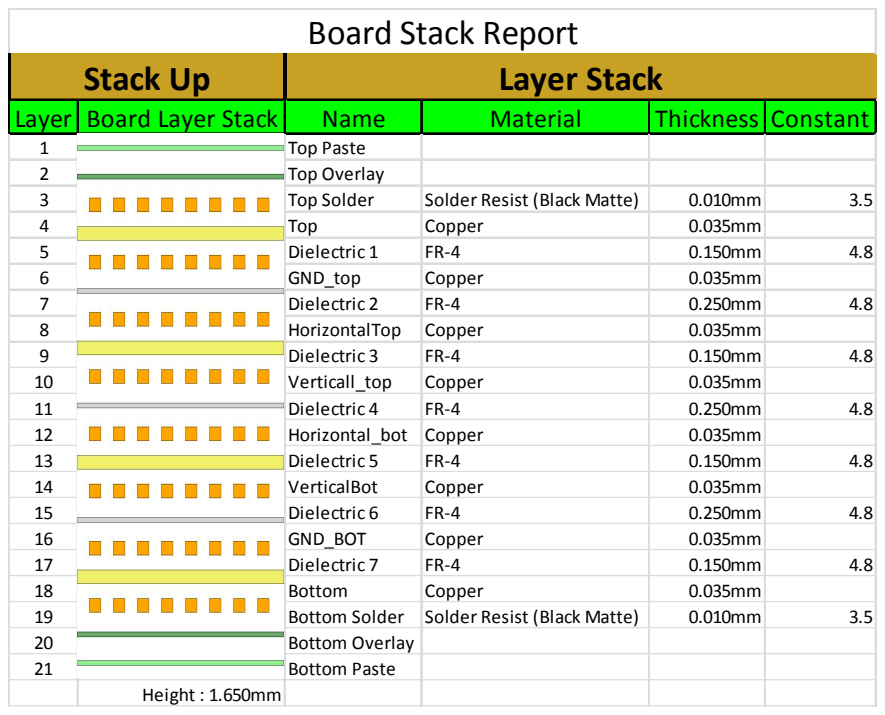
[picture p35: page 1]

Stack Up | Layer Stack
Layer | Board Layer Stack | Name | Material | Thickness | Constant
1 | | Top Paste
2 | | Top Overlay
3 | | Top Solder | Solder Resist (Black Matte) | 0.010mm | 3.5
4 | | Top | Copper | 0.035mm
5 | | Dielectric 1 | FR-4 | 0.150mm | 4.8
6 | | GND_top | Copper | 0.035mm
7 | | Dielectric 2 | FR-4 | 0.250mm | 4.8
8 | | HorizontalTop | Copper | 0.035mm
9 | | Dielectric 3 | FR-4 | 0.150mm | 4.8
10 | | Verticall_top | Copper | 0.035mm
11 | | Dielectric 4 | FR-4 | 0.250mm | 4.8
12 | | Horizontal_bot | Copper | 0.035mm
13 | | Dielectric 5 | FR-4 | 0.150mm | 4.8
14 | | VerticalBot | Copper | 0.035mm
15 | | Dielectric 6 | FR-4 | 0.250mm | 4.8
16 | | GND_BOT | Copper | 0.035mm
17 | | Dielectric 7 | FR-4 | 0.150mm | 4.8
18 | | Bottom | Copper | 0.035mm
19 | | Bottom Solder | Solder Resist (Black Matte) | 0.010mm | 3.5
20 | | Bottom Overlay
21 | | Bottom Paste

Height : 1.650mm

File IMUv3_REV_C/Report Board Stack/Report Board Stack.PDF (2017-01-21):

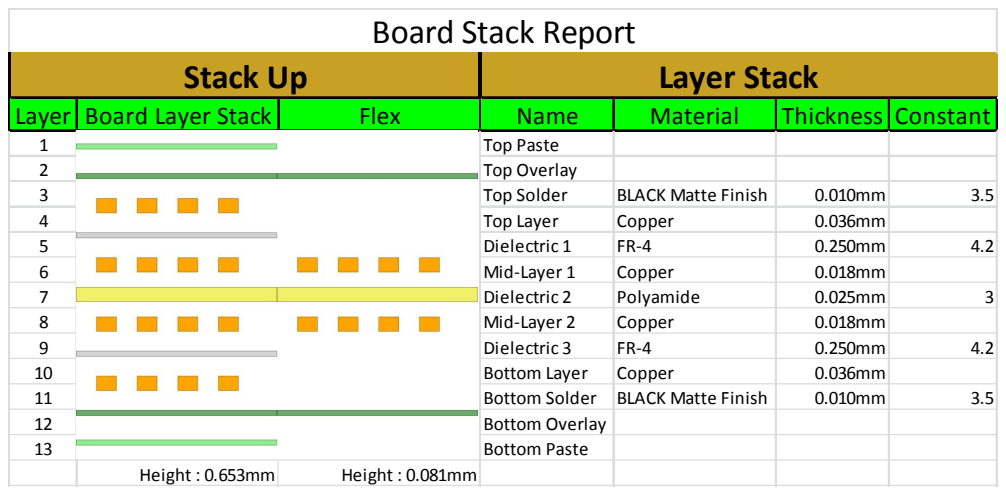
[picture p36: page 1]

Stack Up | Layer Stack

Layer | Board Layer Stack | Flex | Name | Material | Thickness | Constant
1 | | | Top Paste
2 | | | Top Overlay
3 | | | Top Solder | BLACK Matte Finish | 0.010mm | 3.5
4 | | | Top Layer | Copper | 0.036mm
5 | | | Dielectric 1 | FR-4 | 0.250mm | 4.2
6 | | | Mid-Layer 1 | Copper | 0.018mm
7 | | | Dielectric 2 | Polyamide | 0.025mm | 3
8 | | | Mid-Layer 2 | Copper | 0.018mm
9 | | | Dielectric 3 | FR-4 | 0.250mm | 4.2
10 | | | Bottom Layer | Copper | 0.036mm
11 | | | Bottom Solder | BLACK Matte Finish | 0.010mm | 3.5
12 | | | Bottom Overlay
13 | | | Bottom Paste

Height : 0.653mm | Height : 0.081mm

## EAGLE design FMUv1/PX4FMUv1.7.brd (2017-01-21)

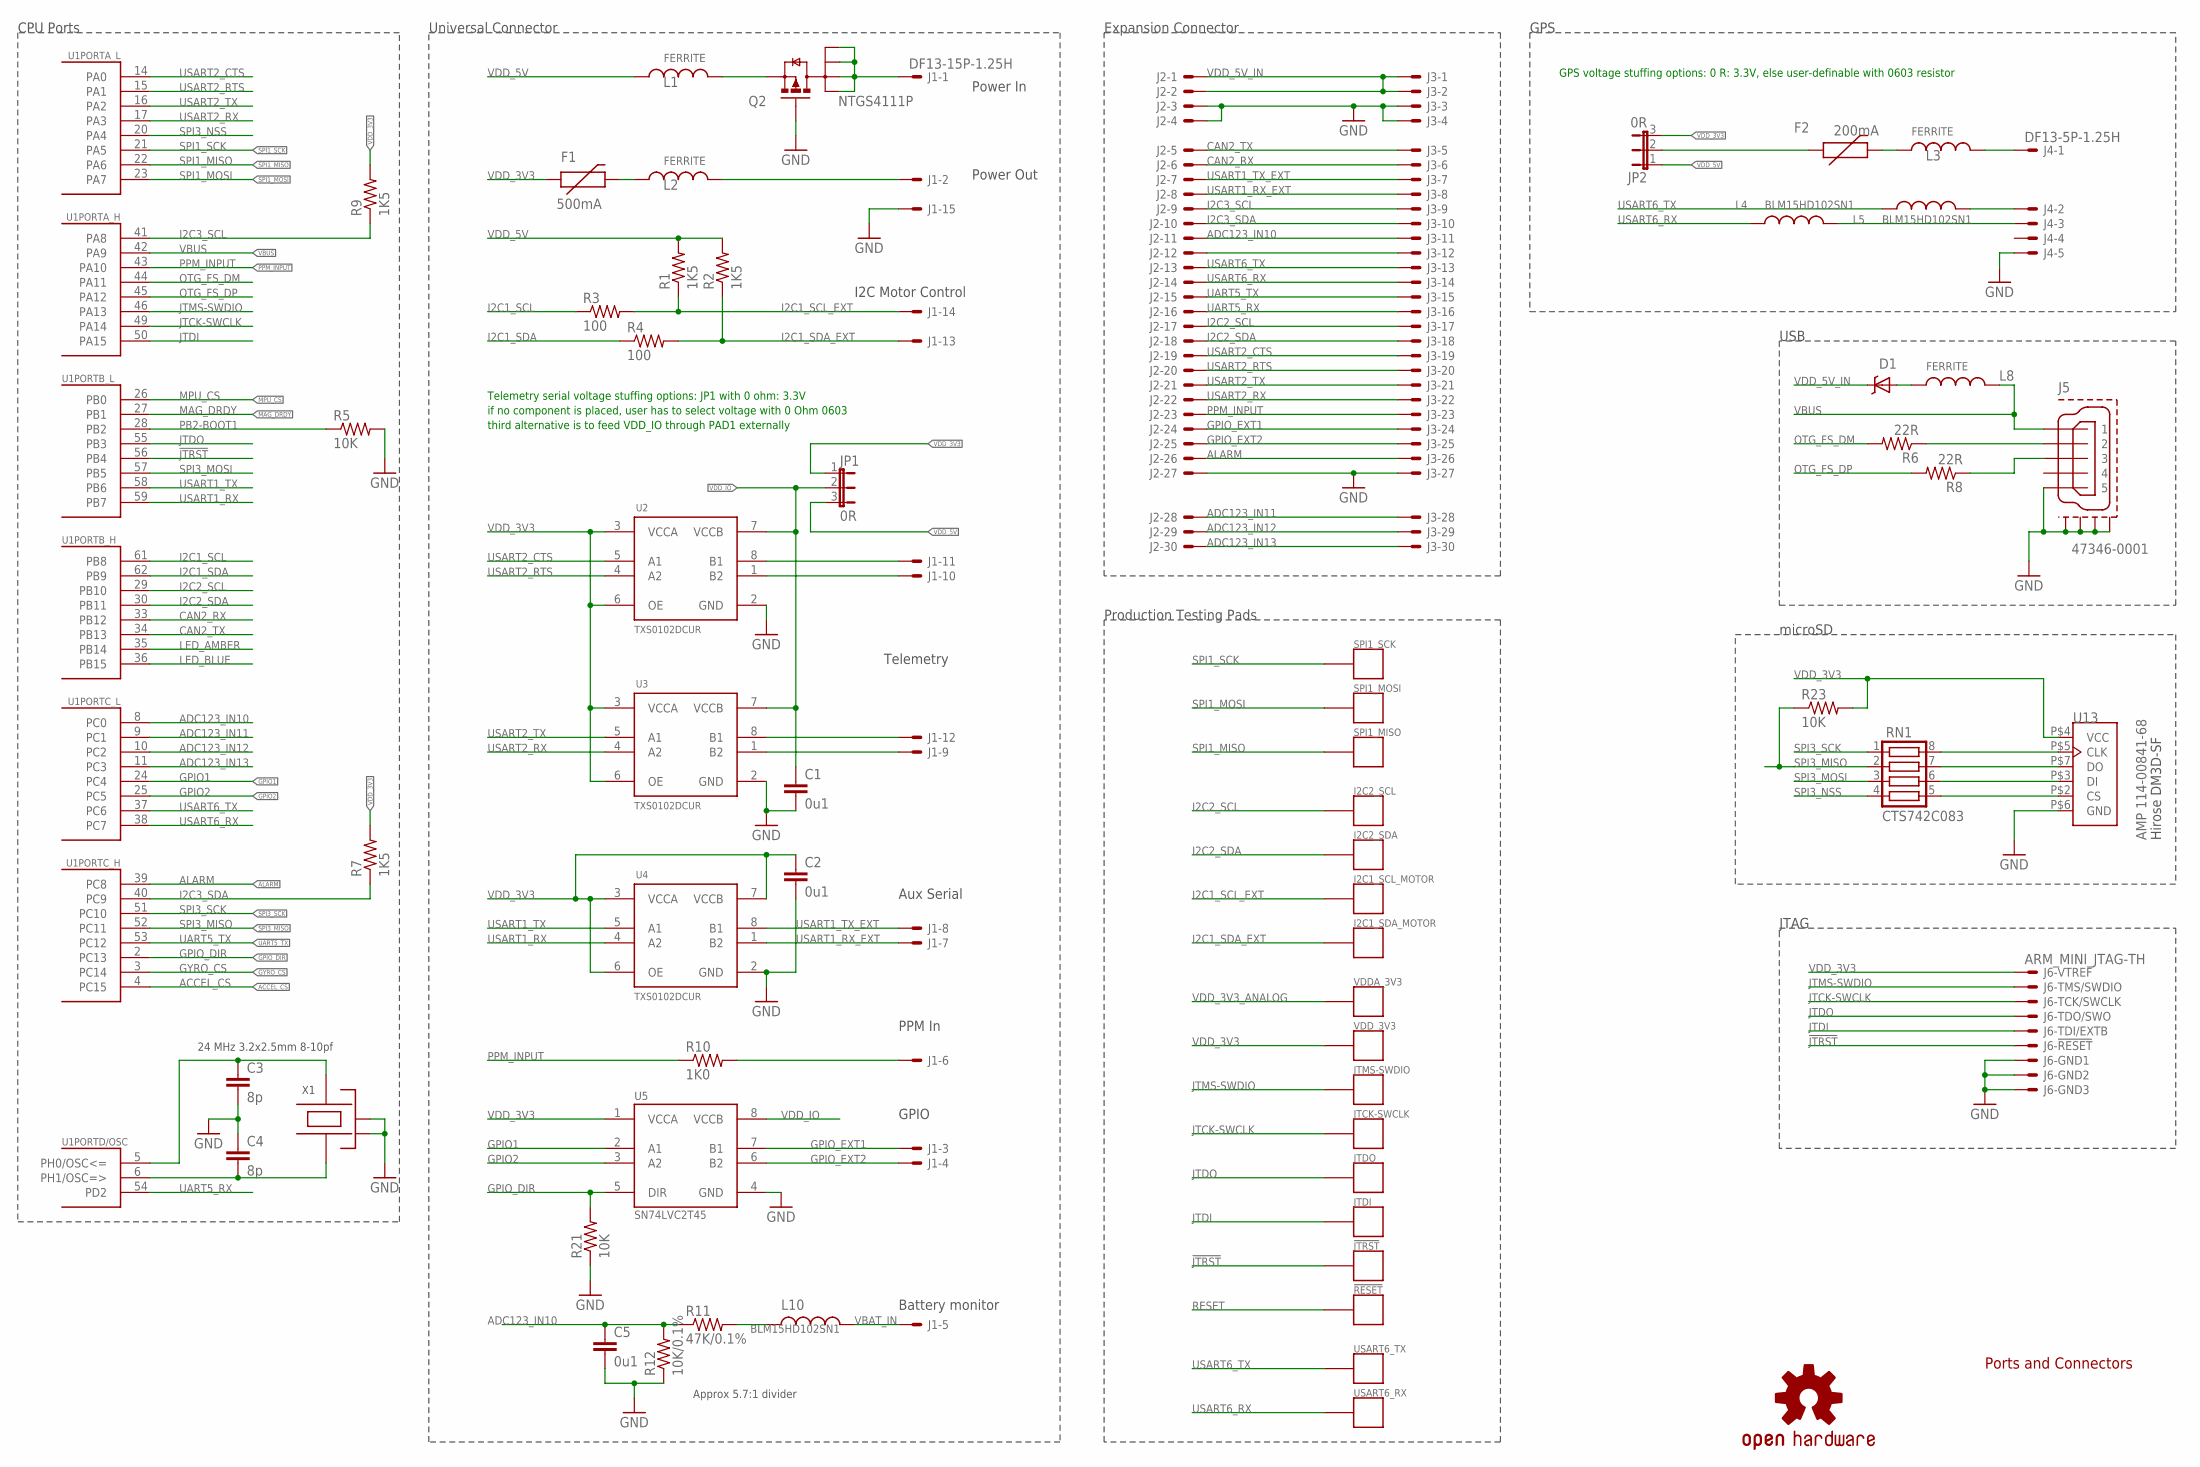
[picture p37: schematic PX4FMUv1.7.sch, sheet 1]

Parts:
!JTRST: PAD.04; PAD.04X.04; PARTNO *
!RESET: PAD.04; PAD.04X.04; PARTNO *
C1, C2, C5: 0u1; 0402-CAP; PARTNO CC0402ZRY5V7BB104
C3, C4: 8p; 0402-CAP; PARTNO C1005C0G1H080C
D1: MSS1P4-M3; MICROSMP; PARTNO MSS1P4-M3/89A
F1: 500mA; 0402-PTC; PARTNO MF-FSMF050X-2
F2: 200mA; 0402-PTC; PARTNO MF-FSMF020X-2
I2C1_SCL_MOTOR, I2C1_SDA_MOTOR, I2C2_SCL: PAD.03; PAD.03X.03; PARTNO *
I2C2_SDA: PAD.04; PAD.04X.04; PARTNO *
J1: DF13-15P-1.25H; DF13A-15P-1.25H; PARTNO DF13A-15P-1.25H(20)
J2: HEADER_2X15-REV; HEADER_2MM_2X15_REVERSE; PARTNO 953230-2000-AR-PR
J3: HEADER_2X15; HEADER_2MM_2X15; PARTNO 953230-2000-AR-PR
J4: DF13-5P-1.25H; DF13A-5P-1.25H; PARTNO DF13A-5P-1.25H(20)
J5: 47346-0001; MOLEX-47346-0001; PARTNO 47346-0001
J6: ARM_MINI_JTAG-TH; FTSH-105-01-XXX-DV; PARTNO M50-3900542
JP1, JP2: 0R; SJ_3_0603_PASTE1&2; PARTNO RMCF0402ZT0R00
JTCK-SWCLK: PAD.04; PAD.04X.04; PARTNO *
JTDI: PAD.04; PAD.04X.04; PARTNO *
JTDO: PAD.04; PAD.04X.04; PARTNO *
JTMS-SWDIO: PAD.04; PAD.04X.04; PARTNO *
L1, L2, L3, L8: FERRITE; 0402-IND; PARTNO BKP1005HS121-T
L4, L5, L10: BLM15HD102SN1; 0402-IND; PARTNO BLM15HD102SN1
Q2: NTGS4111P; TSOP-6; PARTNO NTGS4111P
R1, R2, R7, R9: 1K5; 0402-RES; PARTNO RMCF0402JT1K50
R3, R4: 100; 0402-RES; PARTNO RMCF0402JT100R
R5, R21, R23: 10K; 0402-RES; PARTNO RMCF0402FT10K0
R6, R8: 22R; 0402-RES; PARTNO RMCF0402JT22R0
R10: 1K0; 0402-RES; PARTNO RMCF0402JT1K00
R11: 47K/0.1%; 0402-RES; PARTNO ERA-2AEB473X
R12: 10K/0.1%; 0402-RES; PARTNO ERA-2AEB103X
RN1: CTS742C083; PARTNO TC164-JR-07100RL
SPI1_MISO, SPI1_MOSI, SPI1_SCK: PAD.04; PAD.04X.04; PARTNO *
U1: STM32F405RGT6; TQFP64; PARTNO STM32F405RGT6
U2, U3, U4: TXS0102DCUR; TI-DCU; PARTNO TXS0102DCUR
U5: SN74LVC2T45; TI-DCU; PARTNO SN74LVC2T45
U13: AMP 114-00841-68; AMPHENOL_114-00841-68; PARTNO 114-00841-68
U$7: OSHW-LOGOS; OSHW-LOGO-S; PARTNO *
USART6_RX, USART6_TX: PAD.04; PAD.04X.04; PARTNO *
VDDA_3V3: PAD.04; PAD.04X.04; PARTNO *
VDD_3V3: PAD.04; PAD.04X.04; PARTNO *
X1: 24 MHz 3.2x2.5mm 8-10pf; OSCILLATOR-3.2X2.5; PARTNO NX3225SA-24.000000MHZ

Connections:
!JTRST: !JTRST.P$1, J6.10, U1.56 (PB4)
ACCEL_CS: U1.4 (PC15); also elsewhere on the board
ADC123_IN10: C5.1, J2.11, J3.11, R11.1, R12.2, U1.8 (PC0)
ADC123_IN11: J2.28, J3.28, U1.9 (PC1)
ADC123_IN12: J2.29, J3.29, U1.10 (PC2)
ADC123_IN13: J2.30, J3.30, U1.11 (PC3); also elsewhere on the board
ALARM: J2.26, J3.26, U1.39 (PC8); also elsewhere on the board
CAN2_RX: J2.6, J3.6, U1.33 (PB12)
CAN2_TX: J2.5, J3.5, U1.34 (PB13)
GND: C1.2, C2.2, C3.2, C4.1, C5.2, J1.15, J2.3, J2.4, J2.27, J3.3, J3.4, J3.27, J4.5, J5.GND (5), J5.GND1, J5.GND2, J5.GND3, J5.GND4, J6.3, J6.5, J6.9, Q2.3 (G), R5.2, R12.1, R21.1, U2.2 (GND), U3.2 (GND), U4.2 (GND), U5.4 (GND), U13.P$6 (GND), X1.2 (NC_2), X1.4 (NC_4); also elsewhere on the board
GPIO1: U1.24 (PC4), U5.2 (A1)
GPIO2: U1.25 (PC5), U5.3 (A2)
GPIO_DIR: R21.2, U1.2 (PC13), U5.5 (DIR)
GPIO_EXT1: J1.3, J2.24, J3.24, U5.7 (B1)
GPIO_EXT2: J1.4, J2.25, J3.25, U5.6 (B2)
GYRO_CS: U1.3 (PC14); also elsewhere on the board
I2C1_SCL: R3.1, U1.61 (PB8)
I2C1_SCL_EXT: I2C1_SCL_MOTOR.P$1, J1.14, R1.1, R3.2
I2C1_SDA: R4.1, U1.62 (PB9)
I2C1_SDA_EXT: I2C1_SDA_MOTOR.P$1, J1.13, R2.1, R4.2
I2C2_SCL: I2C2_SCL.P$1, J2.17, J3.17, U1.29 (PB10); also elsewhere on the board
I2C2_SDA: I2C2_SDA.P$1, J2.18, J3.18, U1.30 (PB11); also elsewhere on the board
I2C3_SCL: J2.9, J3.9, R9.1, U1.41 (PA8)
I2C3_SDA: J2.10, J3.10, R7.1, U1.40 (PC9)
JTCK-SWCLK: J6.4, JTCK-SWCLK.P$1, U1.49 (PA14)
JTDI: J6.8, JTDI.P$1, U1.50 (PA15)
JTDO: J6.6, JTDO.P$1, U1.55 (PB3)
JTMS-SWDIO: J6.2, JTMS-SWDIO.P$1, U1.46 (PA13)
LED_AMBER: U1.35 (PB14); also elsewhere on the board
LED_BLUE: U1.36 (PB15); also elsewhere on the board
MAG_DRDY: U1.27 (PB1); also elsewhere on the board
MPU_CS: U1.26 (PB0); also elsewhere on the board
unnamed: C4.2, U1.6 (PH1/OSC=>), X1.1
unnamed: C3.1, U1.5 (PH0/OSC<=), X1.3
unnamed: J1.2, L2.2
unnamed: F2.2, L3.1
unnamed: J4.2, L5.2
unnamed: J4.3, L4.2
unnamed: J1.11, U2.8 (B1)
unnamed: J1.10, U2.1 (B2)
unnamed: L1.2, Q2.4 (S)
unnamed: J1.12, U3.8 (B1)
unnamed: J1.9, U3.1 (B2)
unnamed: F2.1, JP2.2
unnamed: J2.12, J3.12
unnamed: RN1.5, U13.P$2 (CS)
unnamed: D1.ANODE (A), L8.1
unnamed: J4.1, L3.2
unnamed: RN1.6, U13.P$3 (DI)
unnamed: F1.2, L2.1
unnamed: RN1.7, U13.P$7 (DO)
unnamed: RN1.8, U13.P$5 (CLK)
unnamed: L10.1, R11.2
unnamed: J1.1, Q2.1 (D), Q2.2 (D1), Q2.5 (D2), Q2.6 (D3)
OTG_DM: J5.D- (2), R6.1
OTG_DP: J5.D+ (3), R8.1
OTG_FS_DM: R6.2, U1.44 (PA11)
OTG_FS_DP: R8.2, U1.45 (PA12)
PB2-BOOT1: R5.1, U1.28 (PB2)
PPM_INPUT: J2.23, J3.23, R10.1, U1.43 (PA10)
PPM_INPUT_CON: J1.6, R10.2
RESET: !RESET.P$1; also elsewhere on the board
SPI1_MISO: SPI1_MISO.P$1, U1.22 (PA6); also elsewhere on the board
SPI1_MOSI: SPI1_MOSI.P$1, U1.23 (PA7); also elsewhere on the board
SPI1_SCK: SPI1_SCK.P$1, U1.21 (PA5); also elsewhere on the board
SPI3_MISO: R23.1, RN1.2, U1.52 (PC11)
SPI3_MOSI: RN1.3, U1.57 (PB5)
SPI3_NSS: RN1.4, U1.20 (PA4)
SPI3_SCK: RN1.1, U1.51 (PC10)
UART5_RX: J2.16, J3.16, U1.54 (PD2)
UART5_TX: J2.15, J3.15, U1.53 (PC12)
USART1_RX: U1.59 (PB7), U4.4 (A2)
USART1_RX_EXT: J1.7, J2.8, J3.8, U4.1 (B2)
USART1_TX: U1.58 (PB6), U4.5 (A1)
USART1_TX_EXT: J1.8, J2.7, J3.7, U4.8 (B1)
USART2_CTS: J2.19, J3.19, U1.14 (PA0), U2.5 (A1)
USART2_RTS: J2.20, J3.20, U1.15 (PA1), U2.4 (A2)
USART2_RX: J2.22, J3.22, U1.17 (PA3), U3.4 (A2)
USART2_TX: J2.21, J3.21, U1.16 (PA2), U3.5 (A1)
USART6_RX: J2.14, J3.14, L4.1, U1.38 (PC7), USART6_RX.P$1
USART6_TX: J2.13, J3.13, L5.1, U1.37 (PC6), USART6_TX.P$1
VBAT_IN: J1.5, L10.2; also elsewhere on the board
VBUS: J5.VBUS (1), L8.2, U1.42 (PA9)
VDD_3V3: C2.1, F1.1, J6.1, JP1.1, JP2.3, R7.2, R9.2, R23.2, U2.3 (VCCA), U2.6 (OE), U3.3 (VCCA), U3.6 (OE), U4.3 (VCCA), U4.6 (OE), U4.7 (VCCB), U5.1 (VCCA), U13.P$4 (VCC), VDD_3V3.P$1; also elsewhere on the board
VDD_3V3_ANALOG: VDDA_3V3.P$1; also elsewhere on the board
VDD_5V: JP1.3, JP2.1, L1.1, R1.2, R2.2; also elsewhere on the board
VDD_5V_IN: D1.CATHODE (C), J2.1, J2.2, J3.1, J3.2; also elsewhere on the board
VDD_IO: C1.1, JP1.2, U2.7 (VCCB), U3.7 (VCCB), U5.8 (VCCB)

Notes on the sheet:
Ports and Connectors
Telemetry
I2C Motor Control
Power In
Battery monitor
GPIO
Approx 5.7:1 divider
CPU Ports
Universal Connector
GPS
USB
JTAG
GPS voltage stuffing options: 0 R: 3.3V, else user-definable with 0603 resistor
Telemetry serial voltage stuffing options: JP1 with 0 ohm: 3.3V
Aux Serial
PPM In
Expansion Connector
if no component is placed, user has to select voltage with 0 Ohm 0603
Production Testing Pads
Power Out
microSD
third alternative is to feed VDD_IO through PAD1 externally
Hirose DM3D-SF

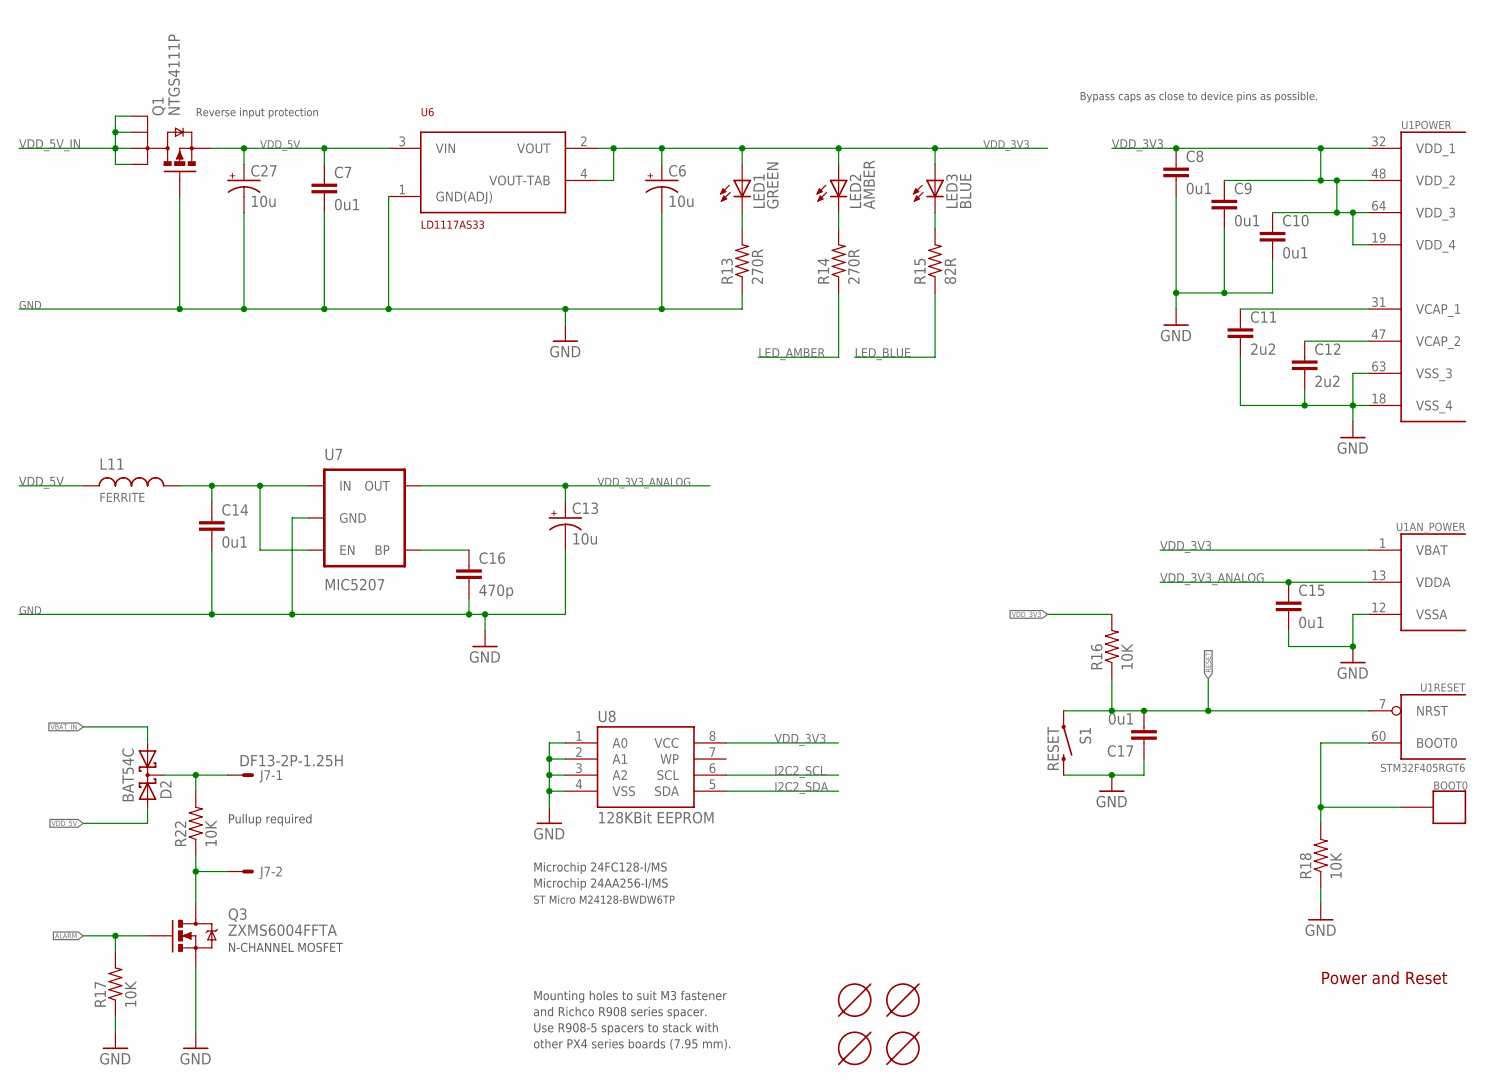
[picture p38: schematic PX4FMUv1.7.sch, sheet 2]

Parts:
BOOT0: PAD.04; PAD.04X.04; PARTNO *
C6, C13, C27: 10u; EIA3216; PARTNO F931A106MAA
C7, C8, C9, C10, C14, C15, C17: 0u1; 0402-CAP; PARTNO CC0402ZRY5V7BB104
C11, C12: 2u2; 0402-CAP; PARTNO C1608Y5V1C225Z
C16: 470p; 0402-CAP; PARTNO CC0402KRX7R9BB471
D2: BAT54C; SOT23-3; PARTNO BAT54C-7-F
J7: DF13-2P-1.25H; DF13A-2P-1.25H; PARTNO DF13-2P-1.25H(20)
L11: FERRITE; 0402-IND; PARTNO BKP1005HS121-T
LED1: GREEN; LED-0603; PARTNO LNJ337W83RA
LED2: AMBER; LED-0603; PARTNO LNJ437W84RA
LED3: BLUE; LED-0603; PARTNO LNJ937W8CRA
Q1: NTGS4111P; TSOP-6; PARTNO NTGS4111P
Q3: ZXMS6004FFTA; SOT23-3; PARTNO ZXMS6004FFTA
R13, R14: 270R; 0402-RES; PARTNO RC0402JR-07270RL
R15: 82R; 0402-RES; PARTNO RC0402JR-0782RL
R16, R17, R18, R22: 10K; 0402-RES; PARTNO RMCF0402FT10K0
S1: RESET; EVQP7J01K; PARTNO EVQP7J01K
U1: STM32F405RGT6; TQFP64; PARTNO STM32F405RGT6
U6: LD1117AS33; SOT-223; PARTNO LD1117AS33
U7: MIC5207; SOT23-5; PARTNO MIC5207-3.3YM5
U8: 128KBit EEPROM; MSOP-8; PARTNO 24FC128-I/MS
U$1, U$2, U$3, U$4: MOUNT-HOLE3.1MM; MOUNT-HOLE3.1; PARTNO *

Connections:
ALARM: Q3.1 (G), R17.2; also elsewhere on the board
BOOT0: BOOT0.P$1, R18.2, U1.60 (BOOT0)
GND: C6.C (-), C7.2, C8.2, C9.2, C10.2, C11.2, C12.2, C13.C (-), C14.2, C15.2, C16.2, C17.1, C27.C (-), Q1.3 (G), Q3.2 (S), R13.1, R17.1, R18.1, S1.B3 (2), U1.12 (VSSA), U1.18 (VSS_4), U1.63 (VSS_3), U6.1 (GND(ADJ)), U7.2 (GND), U8.1 (A0), U8.2 (A1), U8.3 (A2), U8.4 (VSS); also elsewhere on the board
I2C2_SCL: U8.6 (SCL); also elsewhere on the board
I2C2_SDA: U8.5 (SDA); also elsewhere on the board
LED_AMBER: R14.1; also elsewhere on the board
LED_BLUE: R15.1; also elsewhere on the board
unnamed: D2.3 (CC), J7.1, R22.2
unnamed: C16.1, U7.4 (BP)
unnamed: J7.2, Q3.3 (D), R22.1
unnamed: LED3.C, R15.2
unnamed: LED1.C, R13.2
unnamed: LED2.C, R14.2
unnamed: C14.1, L11.2, U7.1 (IN), U7.3 (EN)
RESET: C17.2, R16.1, S1.A1 (1), U1.7 (NRST); also elsewhere on the board
VBAT_IN: D2.1 (A1); also elsewhere on the board
VCAP_1: C11.1, U1.31 (VCAP_1)
VCAP_2: C12.1, U1.47 (VCAP_2)
VDD_3V3: C6.A (+), C8.1, C9.1, C10.1, LED1.A, LED2.A, LED3.A, R16.2, U1.1 (VBAT), U1.19 (VDD_4), U1.32 (VDD_1), U1.48 (VDD_2), U1.64 (VDD_3), U6.2 (VOUT), U6.4 (VOUT-TAB), U8.8 (VCC); also elsewhere on the board
VDD_3V3_ANALOG: C13.A (+), C15.1, U1.13 (VDDA), U7.5 (OUT); also elsewhere on the board
VDD_5V: C7.1, C27.A (+), D2.2 (A2), L11.1, Q1.4 (S), U6.3 (VIN); also elsewhere on the board
VDD_5V_IN: Q1.1 (D), Q1.2 (D1), Q1.5 (D2), Q1.6 (D3); also elsewhere on the board

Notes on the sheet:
Power and Reset
Bypass caps as close to device pins as possible.
Microchip 24FC128-I/MS
Microchip 24AA256-I/MS
Mounting holes to suit M3 fastener
and Richco R908 series spacer.
ST Micro M24128-BWDW6TP
Reverse input protection
N-CHANNEL MOSFET
Pullup required
Use R908-5 spacers to stack with
other PX4 series boards (7.95 mm).

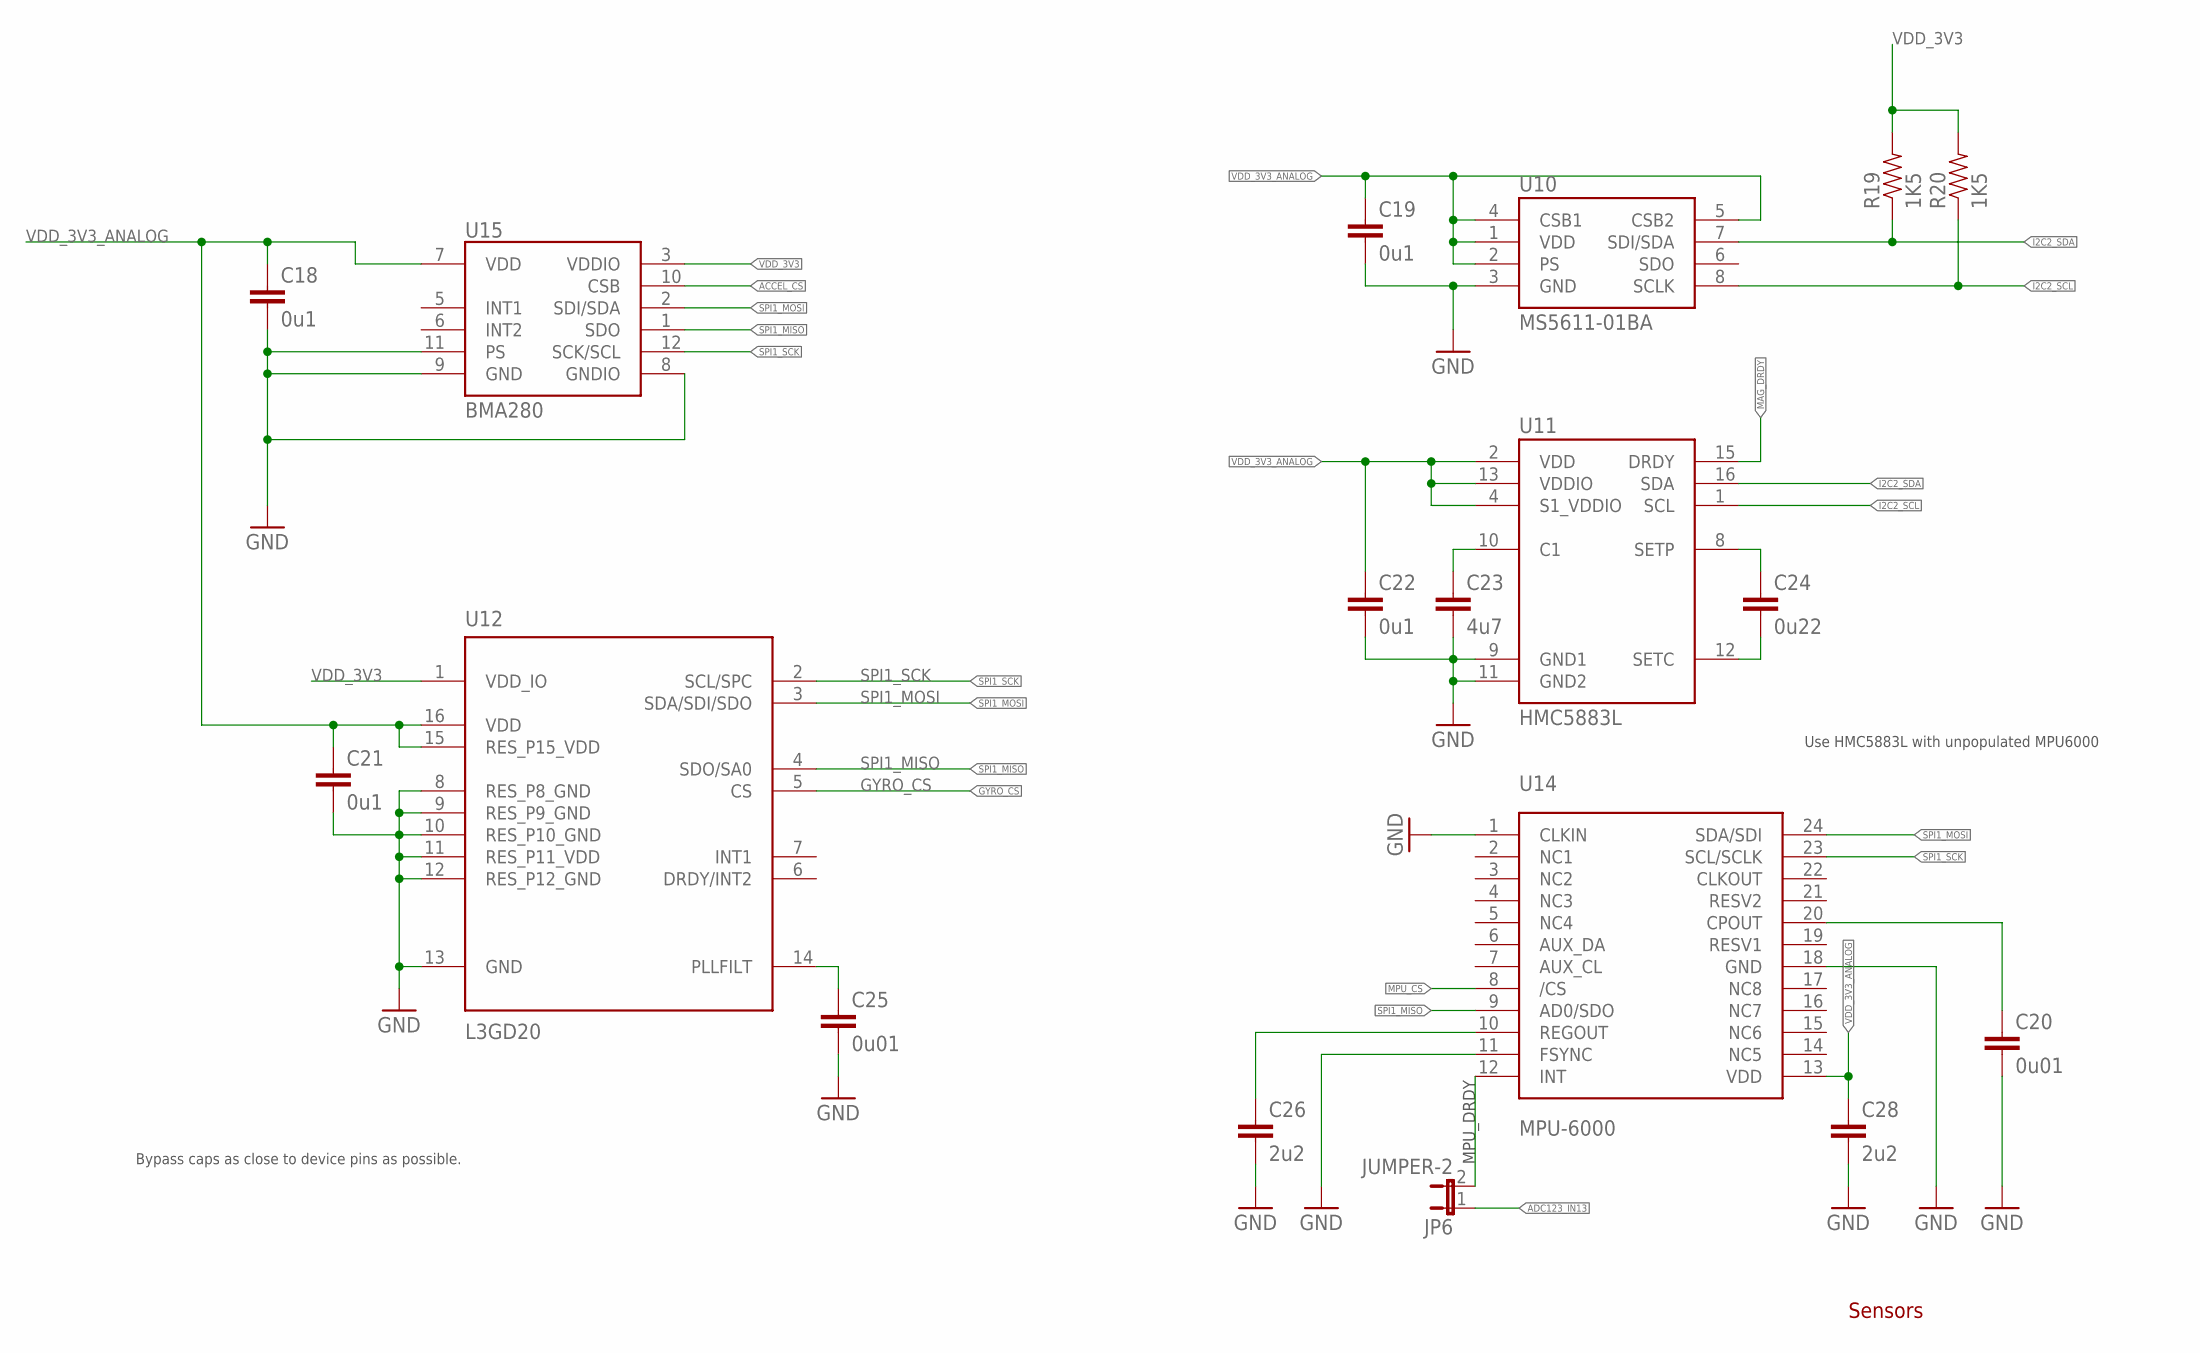
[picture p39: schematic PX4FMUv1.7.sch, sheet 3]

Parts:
C18, C19, C21, C22: 0u1; 0402-CAP; PARTNO CC0402ZRY5V7BB104
C20, C25: 0u01; 0402-CAP; PARTNO CC0402KRX7R7BB103
C23: 4u7; 0402-CAP; PARTNO C1608Y5V0J475Z
C24: 0u22; 0402-CAP; PARTNO C1005Y5V1C224Z
C26, C28: 2u2; 0402-CAP; PARTNO C1608Y5V1C225Z
JP6: JUMPER-2; SJ_2
R19, R20: 1K5; 0402-RES; PARTNO RMCF0402JT1K50
U10: MS5611-01BA; PARTNO MS5611-01BA
U11: HMC5883L; HMC5883L-MAN; PARTNO HMC5883L
U12: L3GD20; L3G4200DH-MAN; PARTNO L3GD20
U14: MPU-6000; QFN-24; PARTNO MPU-6000
U15: BMA280; PARTNO *

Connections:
ACCEL_CS: U15.10 (CSB); also elsewhere on the board
ADC123_IN13: JP6.1; also elsewhere on the board
GND: C18.2, C19.2, C20.2, C21.2, C22.2, C23.2, C25.2, C26.2, C28.2, U10.3 (GND), U11.9 (GND1), U11.11 (GND2), U12.8 (RES_P8_GND), U12.9 (RES_P9_GND), U12.10 (RES_P10_GND), U12.11 (RES_P11_VDD), U12.12 (RES_P12_GND), U12.13 (GND), U14.1 (CLKIN), U14.11 (FSYNC), U14.18 (GND), U15.8 (GNDIO), U15.9 (GND), U15.11 (PS); also elsewhere on the board
GYRO_CS: U12.5 (CS); also elsewhere on the board
I2C2_SCL: R20.1, U10.8 (SCLK), U11.1 (SCL); also elsewhere on the board
I2C2_SDA: R19.1, U10.7 (SDI/SDA), U11.16 (SDA); also elsewhere on the board
MAG_DRDY: U11.15 (DRDY); also elsewhere on the board
MPU_CS: U14.8 (/CS); also elsewhere on the board
unnamed: C24.1, U11.8 (SETP)
unnamed: C24.2, U11.12 (SETC)
unnamed: C25.1, U12.14 (PLLFILT)
unnamed: C23.1, U11.10 (C1)
unnamed: C20.1, U14.20 (CPOUT)
unnamed: C26.1, U14.10 (REGOUT)
unnamed: JP6.2, U14.12 (INT)
SPI1_MISO: U12.4 (SDO/SA0), U14.9 (AD0/SDO), U15.1 (SDO); also elsewhere on the board
SPI1_MOSI: U12.3 (SDA/SDI/SDO), U14.24 (SDA/SDI), U15.2 (SDI/SDA); also elsewhere on the board
SPI1_SCK: U12.2 (SCL/SPC), U14.23 (SCL/SCLK), U15.12 (SCK/SCL); also elsewhere on the board
VDD_3V3: R19.2, R20.2, U12.1 (VDD_IO), U15.3 (VDDIO); also elsewhere on the board
VDD_3V3_ANALOG: C18.1, C19.1, C21.1, C22.1, C28.1, U10.1 (VDD), U10.2 (PS), U10.4 (CSB1), U10.5 (CSB2), U11.2 (VDD), U11.4 (S1_VDDIO), U11.13 (VDDIO), U12.15 (RES_P15_VDD), U12.16 (VDD), U14.13 (VDD), U15.7 (VDD); also elsewhere on the board

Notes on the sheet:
Sensors
Bypass caps as close to device pins as possible.
Use HMC5883L with unpopulated MPU6000
MPU_DRDY

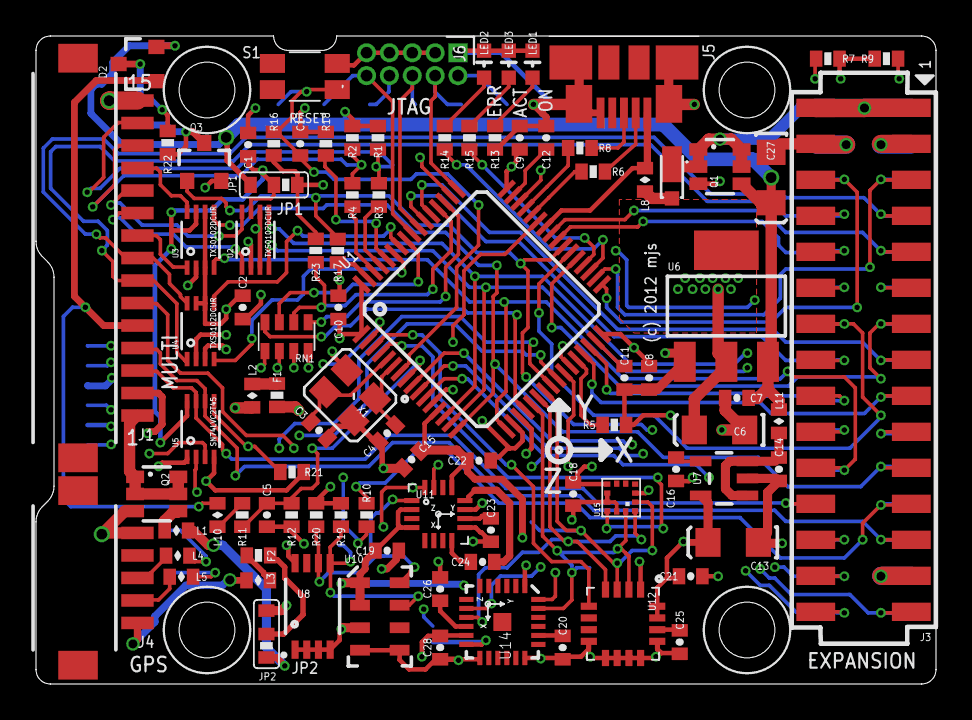
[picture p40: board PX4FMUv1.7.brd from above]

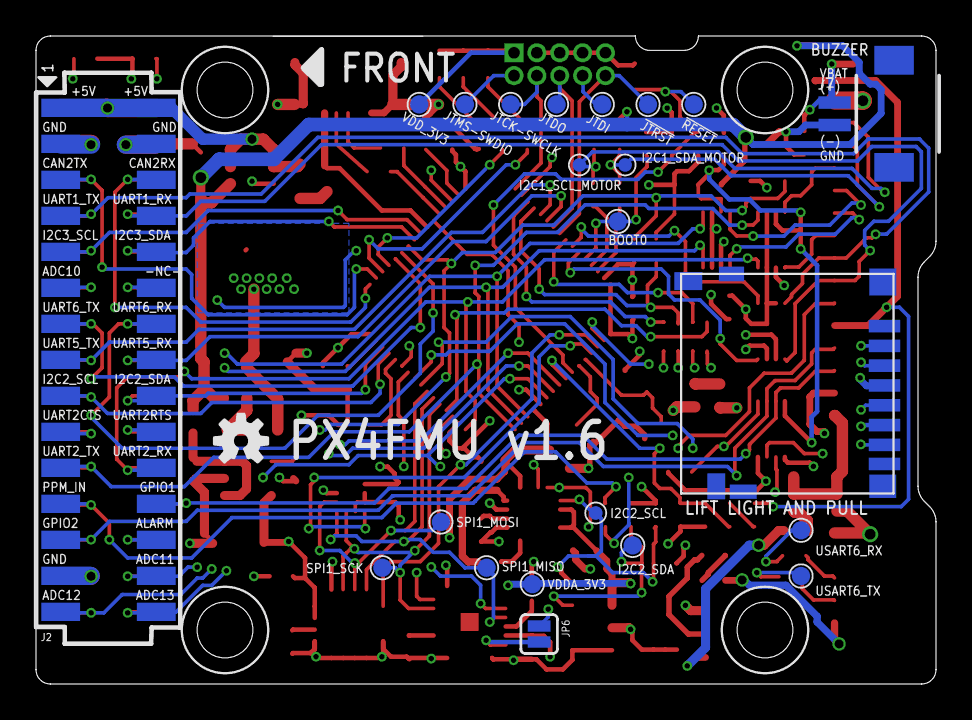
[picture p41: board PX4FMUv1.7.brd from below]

Board: 4 copper layers, 50.0 x 36.0 mm, 119 parts (23 on the bottom side), 105 nets.

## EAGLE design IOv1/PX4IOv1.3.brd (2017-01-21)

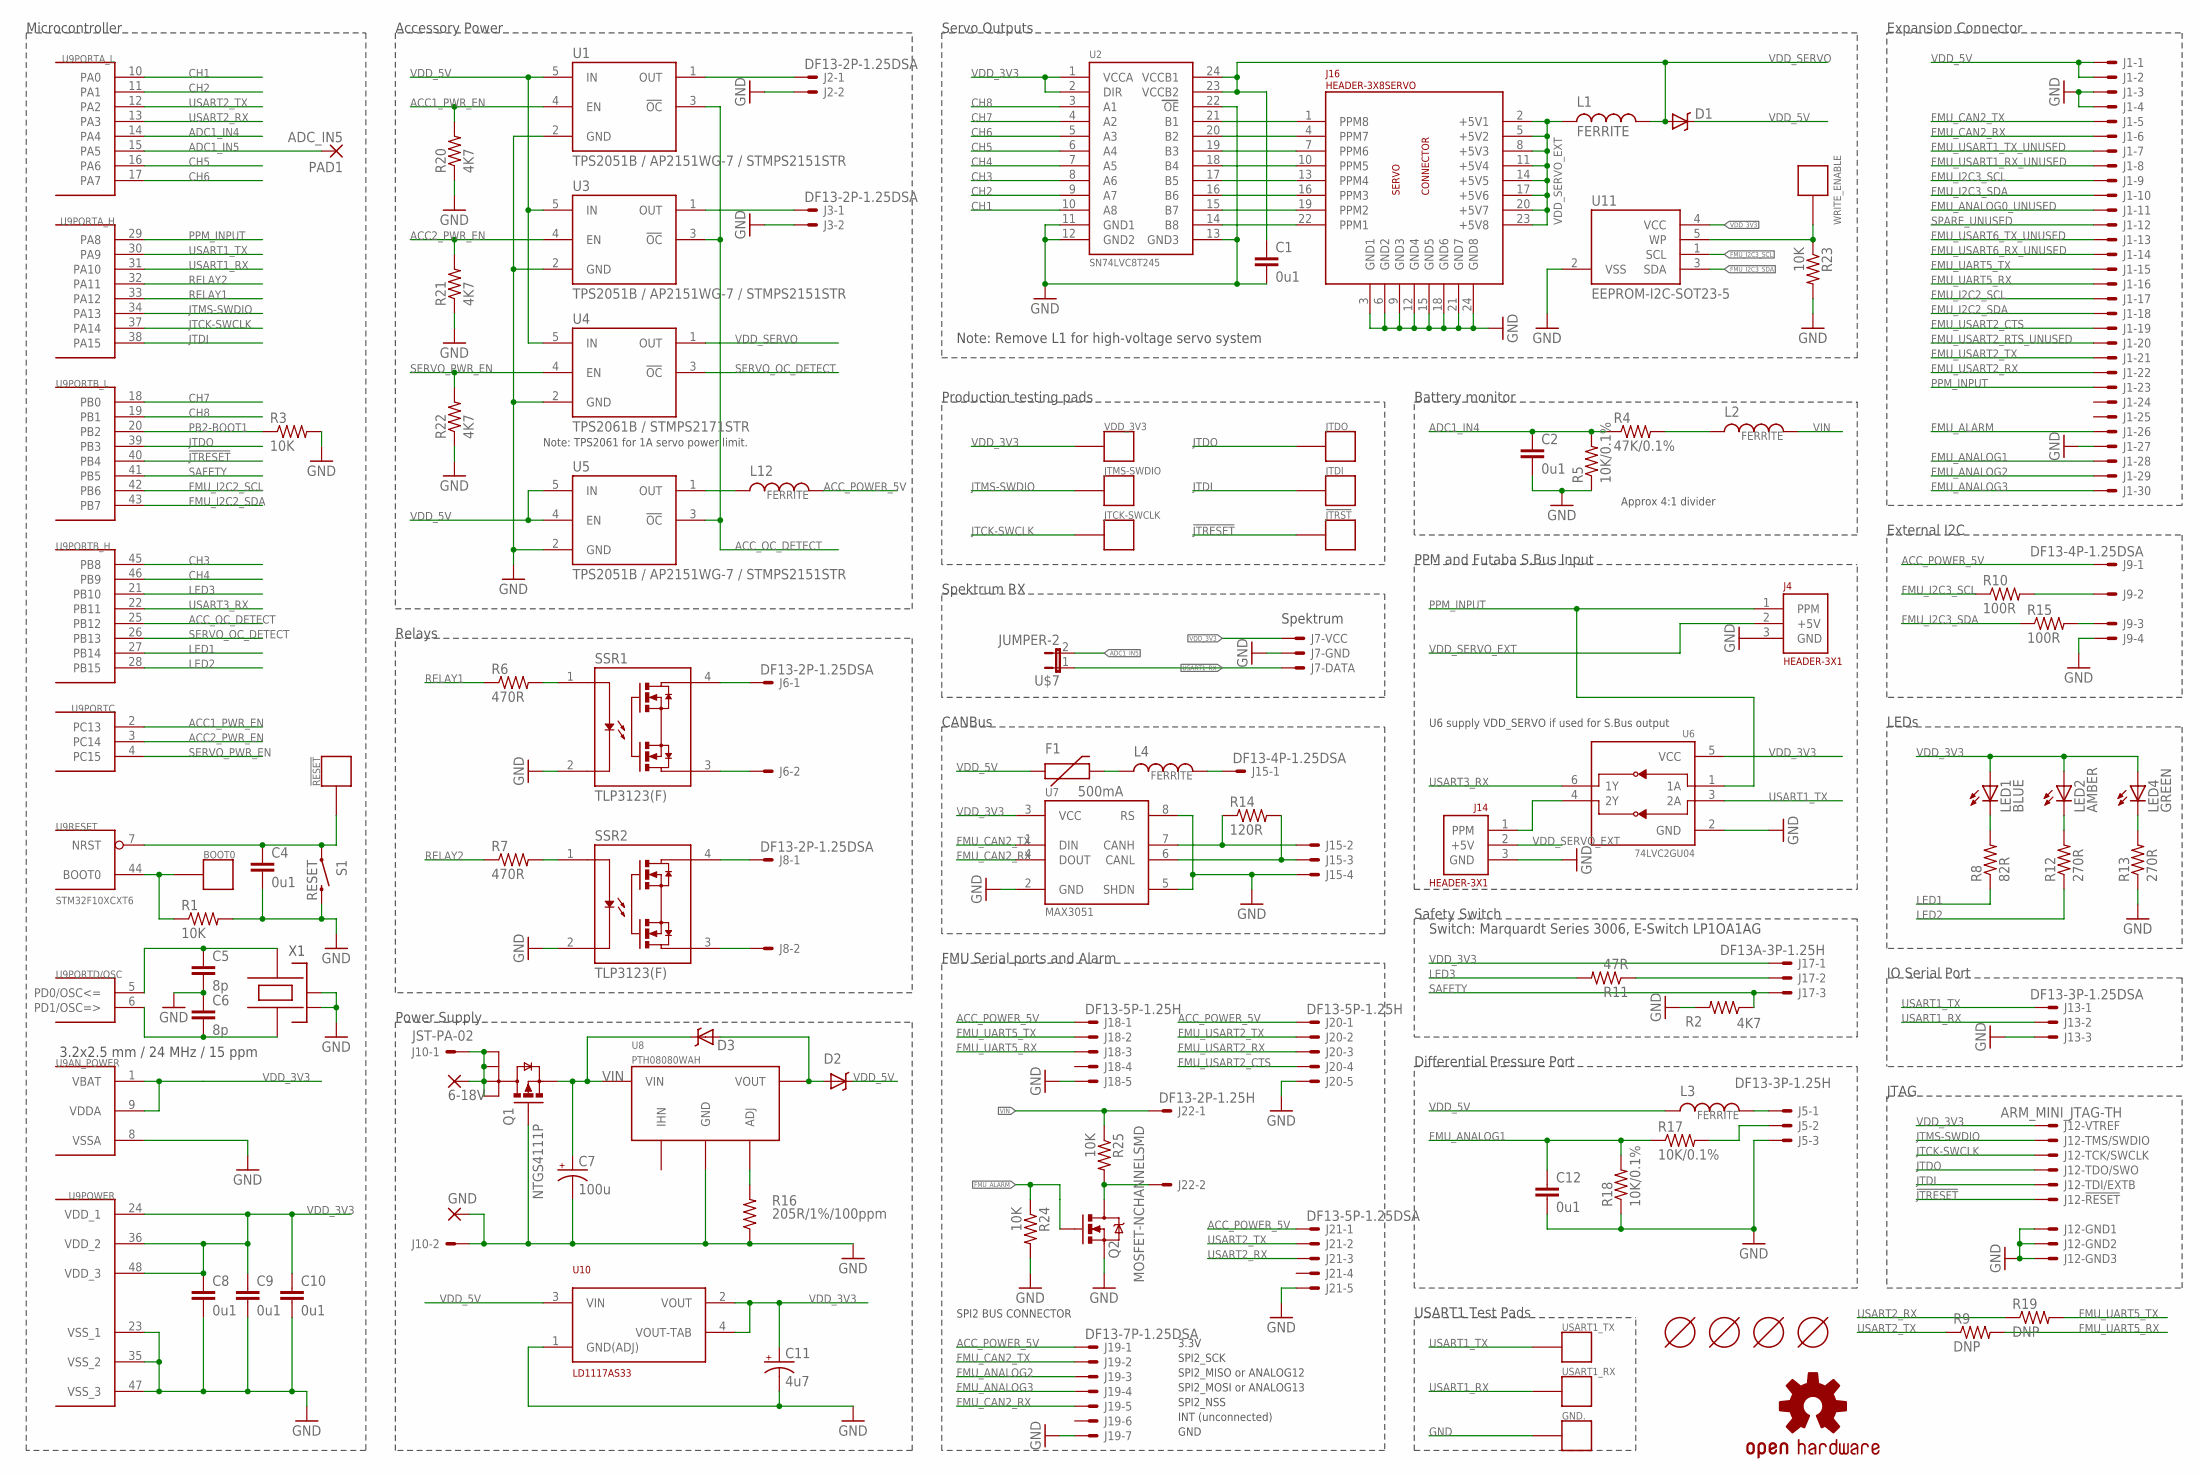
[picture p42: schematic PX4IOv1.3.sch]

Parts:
6-18V: WIREPADSMD3,5-2; 3,5-2; PARTNO *
!JTRST: PAD.04; PAD.04X.04; PARTNO *
!RESET: PAD.03; PAD.03X.03; PARTNO *
BOOT0: PAD.04; PAD.04X.04; PARTNO *
C1, C2, C4, C8, C9, C10, C12: 0u1; 0402-CAP; PARTNO CC0402ZRY5V7BB104
C5, C6: 8p; 0402-CAP; PARTNO C1005C0G1H080C
C7: 100u; EIA7343; PARTNO T491X107K025ZT
C11: 4u7; EIA3216; PARTNO T491A475K010AT
D1, D2: BAT 60A E6327; MICROSMP; PARTNO BAT 60A E6327
D3: MSS1P4-M3/89A; MICROSMP; PARTNO MSS1P4-M3/89A
F1: 500mA; 0603; PARTNO MF-FSMF050X-2
GND: WIREPADSMD3,5-2; 3,5-2; PARTNO *
GND.: PAD.04; PAD.04X.04; PARTNO *
J1: HEADER_2X15-REV; HEADER_2MM_2X15_REVERSE; PARTNO 951230-2520-AR-PR
J2, J3, J6, J8: DF13-2P-1.25DSA; PARTNO DF13-2P-1.25DSA
J4, J14: HEADER-3X1; 3X1RA; PARTNO 53047-02
J5: DF13-3P-1.25H; DF13A-3P-1.25H; PARTNO DF13-3P-1.25H(20)
J7: CONN_SPEKTRUM_RX-TH; B3B-ZR; PARTNO B3B-ZR
J9, J15: DF13-4P-1.25DSA; PARTNO DF13-4P-1.25DSA
J10: JST-PA-02; S02B-PASK-2; PARTNO S02B-PASK-2
J12: ARM_MINI_JTAG-TH; FTSH-105-01-XXX-DV; PARTNO M50-3900542
J13: DF13-3P-1.25DSA; PARTNO DF13-3P-1.25DSA
J16: HEADER-3X8SERVO; 3X8RA; PARTNO *
J17: DF13A-3P-1.25H; PARTNO DF13A-3P-1.25H(20)
J18, J20: DF13-5P-1.25H; DF13A-5P-1.25H; PARTNO DF13A-5P-1.25H(20)
J19: DF13-7P-1.25DSA; PARTNO DF13-7P-1.25DSA(20)
J21: DF13-5P-1.25DSA; PARTNO DF13-5P-1.25DSA(20)
J22: DF13-2P-1.25H; DF13A-2P-1.25H; PARTNO DF13-2P-1.25H(20)
JTCK-SWCLK: PAD.04; PAD.04X.04; PARTNO *
JTDI: PAD.04; PAD.04X.04; PARTNO *
JTDO: PAD.04; PAD.04X.04; PARTNO *
JTMS-SWDIO: PAD.04; PAD.04X.04; PARTNO *
L1, L2, L3, L4, L12: FERRITE; 0402-IND; PARTNO BKP1005HS121-T
LED1: BLUE; LED-0603; PARTNO LNJ937W8CRA
LED2: AMBER; LED-0603; PARTNO LNJ437W84RA
LED4: GREEN; LED-0603; PARTNO LNJ337W83RA
PAD1: ADC_IN5; PAD-2.5-1.8
Q1: NTGS4111P; TSOP-6; PARTNO NTGS4111P
Q2: MOSFET-NCHANNELSMD; SOT23-3; PARTNO ZXMS6004FFTA
R1, R3, R23, R24, R25: 10K; 0402-RES; PARTNO RMCF0402FT10K0
R2, R20, R21, R22: 4K7; 0402-RES; PARTNO RMCF0402JT4K70
R4: 47K/0.1%; 0402-RES; PARTNO RC0402FR-0747KL
R5, R17, R18: 10K/0.1%; 0402-RES; PARTNO RMCF0402FT10K0
R6, R7: 470R; 0402-RES; PARTNO RMCF0402JT470R
R8: 82R; 0402-RES; PARTNO MCR01MZPJ820
R9, R19: DNP; 0402-RES; PARTNO RMCF0402FT10K0
R10, R15: 100R; 0402-RES; PARTNO RMCF0402JT100R
R11: 47R; 0402-RES; PARTNO RMCF0402JT47R0
R12, R13: 270R; 0402-RES; PARTNO MCR01MZPJ271
R14: 120R; 0402-RES; PARTNO P120JCT-ND
R16: 205R/1%/100ppm; 0402-RES; PARTNO ERJ-2RKF2050X
S1: RESET; EVQP7J01K; PARTNO EVQP7J01K
SSR1, SSR2: TLP3123(F); SOP4-2.54; PARTNO TLP3123(F)
U1, U3, U5: TPS2051B / AP2151WG-7 / STMPS2151STR; SOT23-5L; PARTNO AP2151WG-7
U2: SN74LVC8T245; R-PDSO-G24; PARTNO SN74LVC8T245DBQR
U4: TPS2061B / STMPS2171STR; SOT23-5L; PARTNO STMPS2171STR
U6: 74LVC2GU04; SOT363_PHILIPS; PARTNO 74LVC2GU04GW,125
U7: MAX3051; SO08; PARTNO MAX3051ESA+
U8: PTH08080WAH; PTH08080W_TH; PARTNO PTH08080WAH
U9: STM32F10XCXT6; TQFP48; PARTNO STM32F100C8T6B
U10: LD1117AS33; SOT-223; PARTNO LD1117AS33
U11: EEPROM-I2C-SOT23-5; SOT23-5; PARTNO 24LC01BT-I/OT
U$1: OSHW-LOGOS; OSHW-LOGO-S
U$2, U$3, U$4, U$5: MOUNT-HOLE3.1MM; MOUNT-HOLE3.1; PARTNO *
U$7: JUMPER-2; SJ_2
USART1_RX, USART1_TX: PAD.04; PAD.04X.04; PARTNO *
VDD_3V3: PAD.04; PAD.04X.04; PARTNO *
WRITE_ENABLE: PAD.04; PAD.04X.04; PARTNO *
X1: 3.2x2.5 mm / 24 MHz / 15 ppm; OSCILLATOR-3.2X2.5; PARTNO NX3225SA-24.000000MHZ

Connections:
!JTRESET: !JTRST.P$1, J12.10, U9.40 (PB4)
ACC1_PWR_EN: R20.2, U1.4 (EN), U9.2 (PC13)
ACC2_PWR_EN: R21.2, U3.4 (EN), U9.3 (PC14)
ACC_OC_DETECT: U1.3 (!OC), U3.3 (!OC), U5.3 (!OC), U9.25 (PB12)
ACC_POWER_5V: J9.1, J18.1, J19.1, J20.1, J21.1, L12.2
ADC1_IN4: C2.1, R4.1, R5.2, U9.14 (PA4)
ADC1_IN5: PAD1.P$1, U9.15 (PA5), U$7.2
BOOT0: BOOT0.P$1, R1.1, U9.44 (BOOT0)
CH1: U2.10 (A8), U9.10 (PA0)
CH2: U2.9 (A7), U9.11 (PA1)
CH3: U2.8 (A6), U9.45 (PB8)
CH4: U2.7 (A5), U9.46 (PB9)
CH5: U2.6 (A4), U9.16 (PA6)
CH6: U2.5 (A3), U9.17 (PA7)
CH7: U2.4 (A2), U9.18 (PB0)
CH8: U2.3 (A1), U9.19 (PB1)
FMU_ALARM: J1.26, Q2.1 (G), R24.1
FMU_ANALOG0_UNUSED: J1.11
FMU_ANALOG1: C12.1, J1.28, R17.1, R18.2
FMU_ANALOG2: J1.29, J19.3
FMU_ANALOG3: J1.30, J19.4
FMU_CAN2_RX: J1.6, J19.5, U7.4 (DOUT)
FMU_CAN2_TX: J1.5, J19.2, U7.1 (DIN)
FMU_I2C2_SCL: J1.17, U9.42 (PB6)
FMU_I2C2_SDA: J1.18, U9.43 (PB7)
FMU_I2C3_SCL: J1.9, R10.1, U11.1 (SCL)
FMU_I2C3_SDA: J1.10, R15.1, U11.3 (SDA)
FMU_UART5_RX: J1.16, J18.3, R9.2
FMU_UART5_TX: J1.15, J18.2, R19.2
FMU_USART1_RX_UNUSED: J1.8
FMU_USART1_TX_UNUSED: J1.7
FMU_USART2_CTS: J1.19, J20.4
FMU_USART2_RTS_UNUSED: J1.20
FMU_USART2_RX: J1.22, J20.3
FMU_USART2_TX: J1.21, J20.2
FMU_USART6_RX_UNUSED: J1.14
FMU_USART6_TX_UNUSED: J1.13
GND: C1.2, C2.2, C4.2, C5.2, C6.1, C7.C (-), C8.2, C9.2, C10.2, C11.C (-), C12.2, GND.1, GND..P$1, J1.3, J1.4, J1.27, J2.2, J3.2, J4.3 (GND), J5.3, J7.2, J9.4, J10.2, J12.3, J12.5, J12.9, J13.3, J14.3 (GND), J15.4, J16.3 (GND1), J16.6 (GND2), J16.9 (GND3), J16.12 (GND4), J16.15 (GND5), J16.18 (GND6), J16.21 (GND7), J16.24 (GND8), J18.5, J19.7, J20.5, J21.5, Q1.3 (G), Q2.2 (S), R1.2, R2.2, R3.2, R5.1, R13.1, R16.1, R18.1, R20.1, R21.1, R22.1, R23.2, R24.2, S1.B3 (2), SSR1.2, SSR2.2, U1.2 (GND), U2.11 (GND1), U2.12 (GND2), U2.13 (GND3), U2.22 (OE), U3.2 (GND), U4.2 (GND), U5.2 (GND), U6.2 (GND), U7.2 (GND), U7.5 (SHDN), U7.8 (RS), U8.2 (GND), U9.8 (VSSA), U9.23 (VSS_1), U9.35 (VSS_2), U9.47 (VSS_3), U10.1 (GND(ADJ)), U11.2 (VSS), X1.2 (NC_2), X1.4 (NC_4)
JTCK-SWCLK: J12.4, JTCK-SWCLK.P$1, U9.37 (PA14)
JTDI: J12.8, JTDI.P$1, U9.38 (PA15)
JTDO: J12.6, JTDO.P$1, U9.39 (PB3)
JTMS-SWDIO: J12.2, JTMS-SWDIO.P$1, U9.34 (PA13)
LED1: R8.1, U9.27 (PB14)
LED2: R12.1, U9.28 (PB15)
LED3: R11.2, U9.21 (PB10)
unnamed: R7.2, SSR2.1
unnamed: R6.2, SSR1.1
unnamed: J14.1 (PPM), U6.4 (2Y)
unnamed: L12.1, U5.1 (OUT)
unnamed: C6.2, U9.6 (PD1/OSC=>), X1.1
unnamed: C5.1, U9.5 (PD0/OSC<=), X1.3
unnamed: L2.1, R4.2
unnamed: LED1.C, R8.2
unnamed: R16.2, U8.4 (ADJ)
unnamed: J17.2, R11.1
unnamed: R23.1, U11.5 (WP), WRITE_ENABLE.P$1
unnamed: J22.2, Q2.3 (D), R25.2
unnamed: F1.2, L4.1
unnamed: J5.2, R17.2
unnamed: J8.1, SSR2.4
unnamed: J8.2, SSR2.3
unnamed: J6.2, SSR1.3
unnamed: J6.1, SSR1.4
unnamed: J9.3, R15.2
unnamed: J9.2, R10.2
unnamed: J2.1, U1.1 (OUT)
unnamed: J3.1, U3.1 (OUT)
unnamed: LED2.C, R12.2
unnamed: LED4.C, R13.2
unnamed: J15.2, R14.1, U7.7 (CANH)
unnamed: J15.3, R14.2, U7.6 (CANL)
unnamed: J15.1, L4.2
NRST: !RESET.P$1, C4.1, S1.A1 (1), U9.7 (NRST)
PB2-BOOT1: R3.1, U9.20 (PB2)
PPM1: J16.22 (PPM1), U2.14 (B8)
PPM2: J16.19 (PPM2), U2.15 (B7)
PPM3: J16.16 (PPM3), U2.16 (B6)
PPM4: J16.13 (PPM4), U2.17 (B5)
PPM5: J16.10 (PPM5), U2.18 (B4)
PPM6: J16.7 (PPM6), U2.19 (B3)
PPM7: J16.4 (PPM7), U2.20 (B2)
PPM8: J16.1 (PPM8), U2.21 (B1)
PPM_INPUT: J1.23, J4.1 (PPM), U6.1 (1A), U9.29 (PA8)
RELAY1: R6.1, U9.33 (PA12)
RELAY2: R7.1, U9.32 (PA11)
SAFETY: J17.3, R2.1, U9.41 (PB5)
SERVO_OC_DETECT: U4.3 (!OC), U9.26 (PB13)
SERVO_PWR_EN: R22.2, U4.4 (EN), U9.4 (PC15)
SPARE_UNUSED: J1.12
USART1_RX: J7.1, J13.2, U9.31 (PA10), U$7.1, USART1_RX.P$1
USART1_TX: J13.1, U6.3 (2A), U9.30 (PA9), USART1_TX.P$1
USART2_RX: J21.3, R19.1, U9.13 (PA3)
USART2_TX: J21.2, R9.1, U9.12 (PA2)
USART3_RX: U6.6 (1Y), U9.22 (PB11)
VDD_3V3: C8.1, C9.1, C10.1, C11.A (+), J7.3, J12.1, J17.1, LED1.A, LED2.A, LED4.A, U2.1 (VCCA), U2.2 (DIR), U6.5 (VCC), U7.3 (VCC), U9.1 (VBAT), U9.9 (VDDA), U9.24 (VDD_1), U9.36 (VDD_2), U9.48 (VDD_3), U10.2 (VOUT), U10.4 (VOUT-TAB), U11.4 (VCC), VDD_3V3.P$1
VDD_5V: D1.CATHODE (C), D2.CATHODE (C), F1.1, J1.1, J1.2, L3.1, U1.5 (IN), U3.5 (IN), U4.5 (IN), U5.4 (EN), U5.5 (IN), U10.3 (VIN)
VDD_5V_ANALOG: J5.1, L3.2
VDD_SERVO: C1.1, D1.ANODE (A), L1.2, U2.23 (VCCB2), U2.24 (VCCB1), U4.1 (OUT)
VDD_SERVO_EXT: J4.2 (+5V), J14.2 (+5V), J16.2 (+5V1), J16.5 (+5V2), J16.8 (+5V3), J16.11 (+5V4), J16.14 (+5V5), J16.17 (+5V6), J16.20 (+5V7), J16.23 (+5V8), L1.1
VIN: C7.A (+), D3.CATHODE (C), J22.1, L2.2, Q1.4 (S), R25.1, U8.1 (VIN)
VIN_CONTACT: 6-18V.1, J10.1, Q1.1 (D), Q1.2 (D1), Q1.5 (D2), Q1.6 (D3)
VOUT: D2.ANODE (A), D3.ANODE (A), U8.3 (VOUT)

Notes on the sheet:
Note: Remove L1 for high-voltage servo system
Spektrum
Accessory Power
Relays
Power Supply
Servo Outputs
CANBus
Production testing pads
External I2C
Spektrum RX
JTAG
LEDs
FMU Serial ports and Alarm
Expansion Connector
Microcontroller
Note: TPS2061 for 1A servo power limit.
PPM and Futaba S.Bus Input
Differential Pressure Port
Battery monitor
Approx 4:1 divider
U6 supply VDD_SERVO if used for S.Bus output
IO Serial Port
USART1 Test Pads
Safety Switch
Switch: Marquardt Series 3006, E-Switch LP1OA1AG
3.3V
SPI2_SCK
SPI2_MISO or ANALOG12
SPI2_MOSI or ANALOG13
SPI2_NSS
GND
SPI2 BUS CONNECTOR
INT (unconnected)

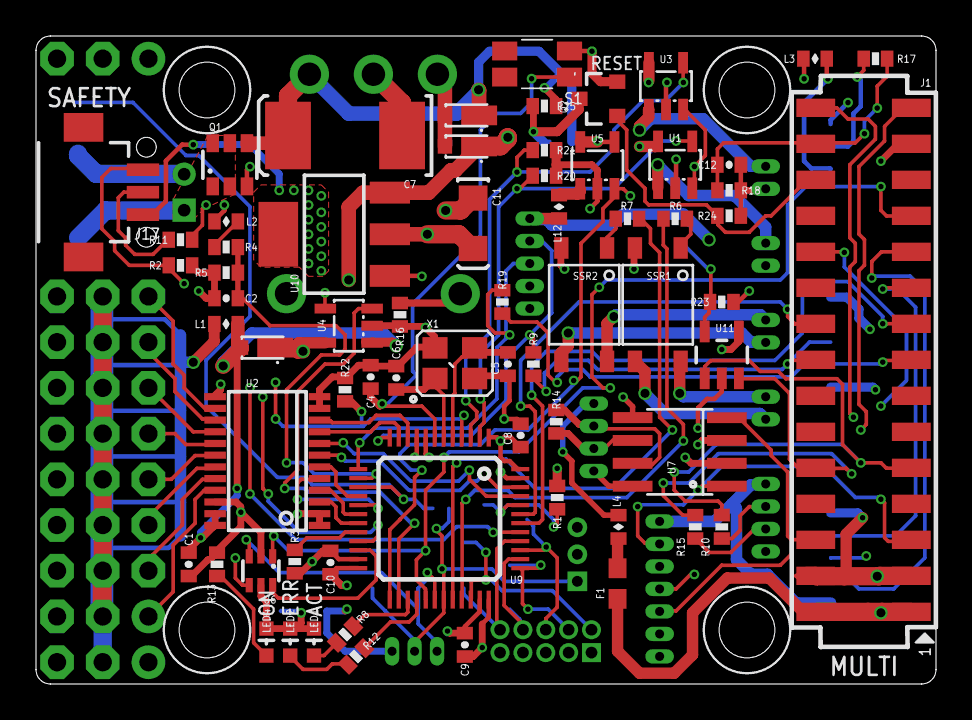
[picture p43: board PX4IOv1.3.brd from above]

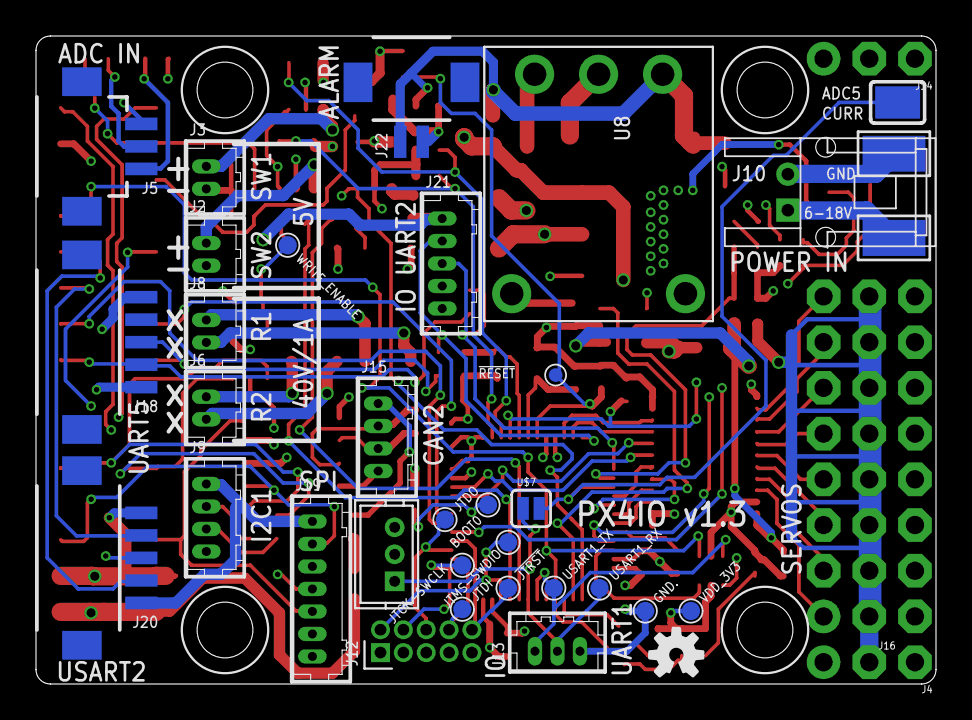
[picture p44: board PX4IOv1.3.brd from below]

Board: 4 copper layers, 50.0 x 36.0 mm, 107 parts (37 on the bottom side), 95 nets.

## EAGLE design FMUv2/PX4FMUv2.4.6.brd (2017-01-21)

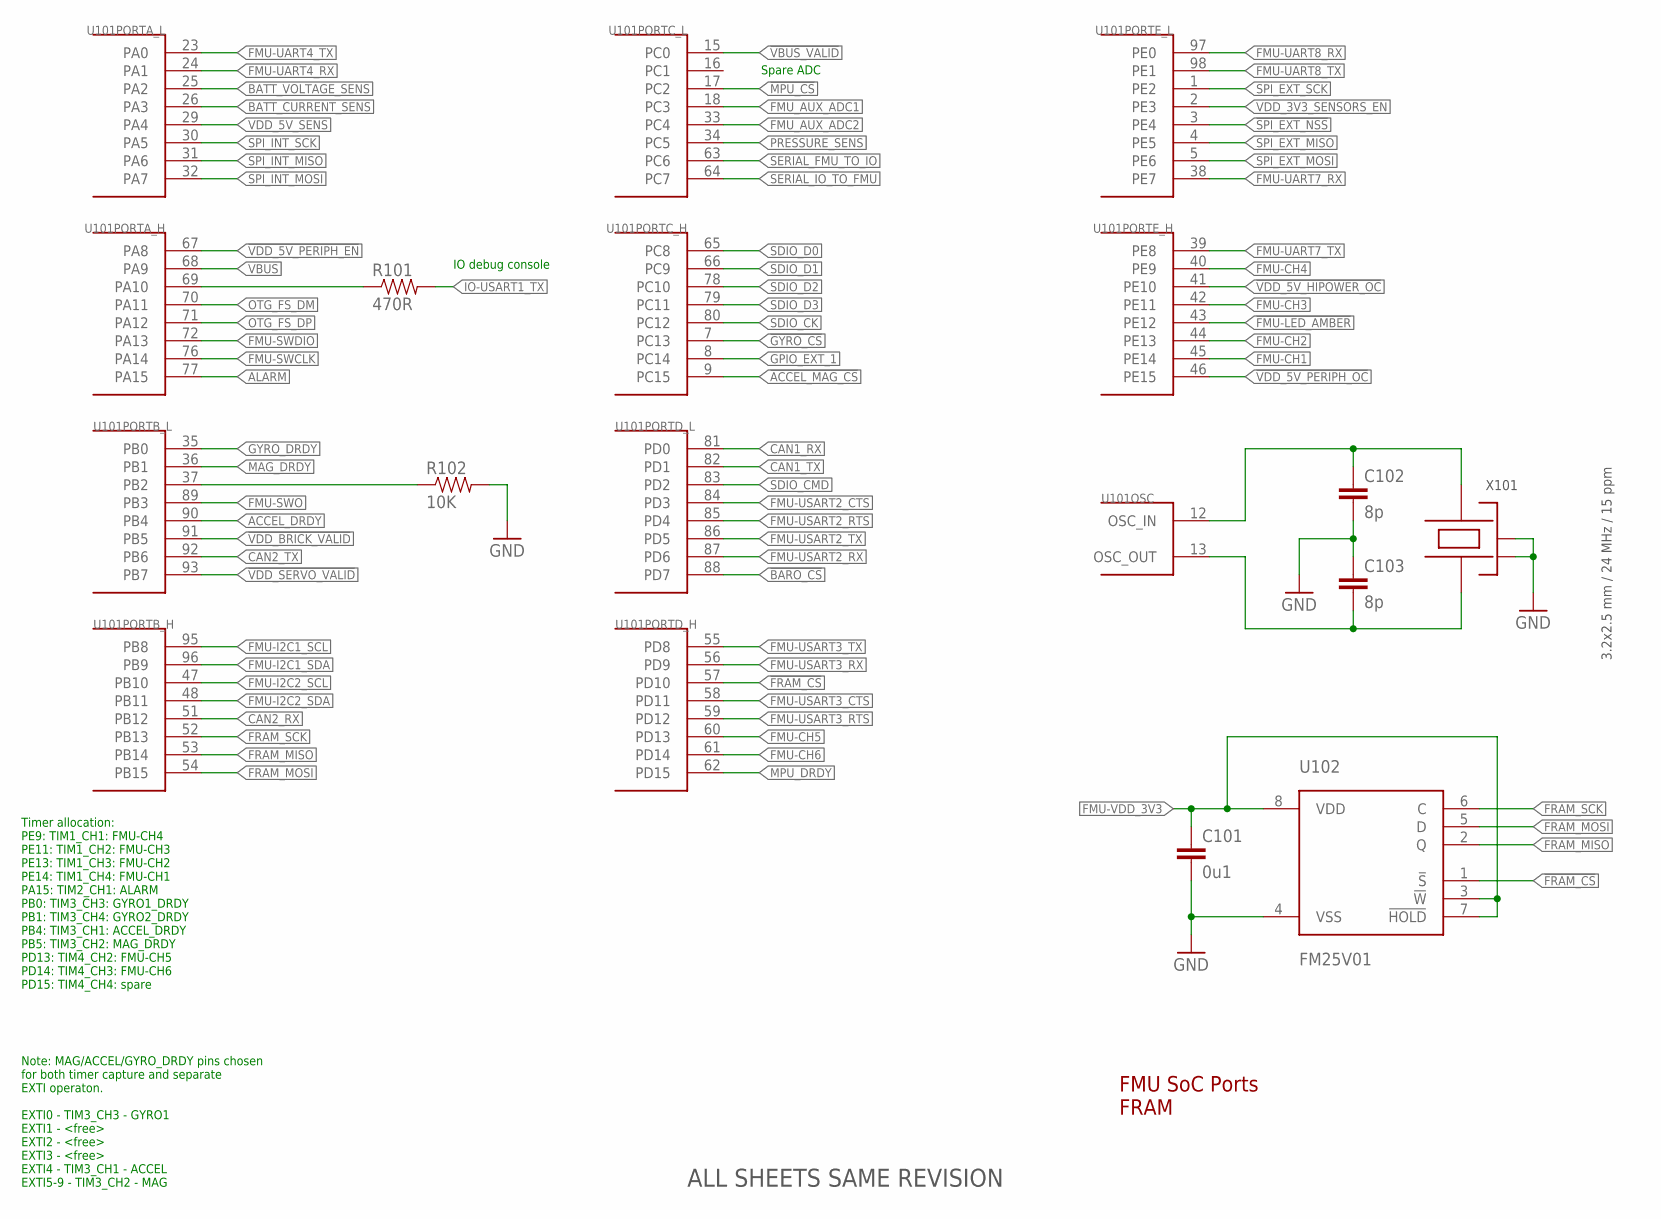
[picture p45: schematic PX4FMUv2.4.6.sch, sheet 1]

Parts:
C101: 0u1; 0402-CAP; PARTNO CC0402ZRY5V7BB104
C102, C103: 8p; 0402-CAP; PARTNO C1005C0G1H080C
R101: 470R; 0402-RES; PARTNO RC0402FR-07470RL
R102: 10K; 0402-RES; PARTNO RC0402FR-0710KL
U101: STM32F4X7VX; TQFP100; PARTNO STM32F427VI
U102: FM25V01; SO08; PARTNO FM25V01-G
X101: 3.2x2.5 mm / 24 MHz / 15 ppm; OSCILLATOR-3.2X2.5; PARTNO NX3225SA-24.000000MHZ

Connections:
!ACCEL_MAG_CS: U101.9 (PC15); also elsewhere on the board
!BARO_CS: U101.88 (PD7); also elsewhere on the board
!FMU-LED_AMBER: U101.43 (PE12); also elsewhere on the board
!FRAM_CS: U101.57 (PD10), U102.1 (!S)
!GYRO_CS: U101.7 (PC13); also elsewhere on the board
!MPU_CS: U101.17 (PC2); also elsewhere on the board
!SPI_EXT_NSS: U101.3 (PE4); also elsewhere on the board
!VBUS_VALID: U101.15 (PC0); also elsewhere on the board
!VDD_5V_HIPOWER_OC: U101.41 (PE10); also elsewhere on the board
!VDD_5V_PERIPH_EN: U101.67 (PA8); also elsewhere on the board
!VDD_5V_PERIPH_OC: U101.46 (PE15); also elsewhere on the board
!VDD_BRICK_VALID: U101.91 (PB5); also elsewhere on the board
!VDD_SERVO_VALID: U101.93 (PB7); also elsewhere on the board
ACCEL_DRDY: U101.90 (PB4); also elsewhere on the board
ALARM: U101.77 (PA15); also elsewhere on the board
BATT_CURRENT_SENS: U101.26 (PA3); also elsewhere on the board
BATT_VOLTAGE_SENS: U101.25 (PA2); also elsewhere on the board
CAN1_RX: U101.81 (PD0); also elsewhere on the board
CAN1_TX: U101.82 (PD1); also elsewhere on the board
CAN2_RX: U101.51 (PB12); also elsewhere on the board
CAN2_TX: U101.92 (PB6); also elsewhere on the board
FMU-CH1: U101.45 (PE14); also elsewhere on the board
FMU-CH2: U101.44 (PE13); also elsewhere on the board
FMU-CH3: U101.42 (PE11); also elsewhere on the board
FMU-CH4: U101.40 (PE9); also elsewhere on the board
FMU-CH5: U101.60 (PD13); also elsewhere on the board
FMU-CH6: U101.61 (PD14); also elsewhere on the board
FMU-I2C1_SCL: U101.95 (PB8); also elsewhere on the board
FMU-I2C1_SDA: U101.96 (PB9); also elsewhere on the board
FMU-I2C2_SCL: U101.47 (PB10); also elsewhere on the board
FMU-I2C2_SDA: U101.48 (PB11); also elsewhere on the board
FMU-SWCLK: U101.76 (PA14); also elsewhere on the board
FMU-SWDIO: U101.72 (PA13); also elsewhere on the board
FMU-SWO: U101.89 (PB3); also elsewhere on the board
FMU-UART4_RX: U101.24 (PA1); also elsewhere on the board
FMU-UART4_TX: U101.23 (PA0); also elsewhere on the board
FMU-UART7_RX: U101.38 (PE7); also elsewhere on the board
FMU-UART7_TX: U101.39 (PE8); also elsewhere on the board
FMU-UART8_RX: U101.97 (PE0); also elsewhere on the board
FMU-UART8_TX: U101.98 (PE1); also elsewhere on the board
FMU-USART2_CTS: U101.84 (PD3); also elsewhere on the board
FMU-USART2_RTS: U101.85 (PD4); also elsewhere on the board
FMU-USART2_RX: U101.87 (PD6); also elsewhere on the board
FMU-USART2_TX: U101.86 (PD5); also elsewhere on the board
FMU-USART3_CTS: U101.58 (PD11); also elsewhere on the board
FMU-USART3_RTS: U101.59 (PD12); also elsewhere on the board
FMU-USART3_RX: U101.56 (PD9); also elsewhere on the board
FMU-USART3_TX: U101.55 (PD8); also elsewhere on the board
FMU-VDD_3V3: C101.P$1 (1), U102.3 (!W), U102.7 (!HOLD), U102.8 (VDD); also elsewhere on the board
FMU_AUX_ADC1: U101.18 (PC3); also elsewhere on the board
FMU_AUX_ADC2: U101.33 (PC4); also elsewhere on the board
FRAM_MISO: U101.53 (PB14), U102.2 (Q)
FRAM_MOSI: U101.54 (PB15), U102.5 (D)
FRAM_SCK: U101.52 (PB13), U102.6 (C)
GND: C101.P$2 (2), C102.P$2 (2), C103.P$1 (1), R102.P$2 (2), U102.4 (VSS), X101.2 (NC_2), X101.4 (NC_4); also elsewhere on the board
GPIO_EXT_1: U101.8 (PC14); also elsewhere on the board
GYRO_DRDY: U101.35 (PB0); also elsewhere on the board
IO-USART1_TX: R101.P$2 (2); also elsewhere on the board
MAG_DRDY: U101.36 (PB1); also elsewhere on the board
MPU_DRDY: U101.62 (PD15); also elsewhere on the board
unnamed: C103.P$2 (2), U101.13 (OSC_OUT), X101.1
unnamed: C102.P$1 (1), U101.12 (OSC_IN), X101.3
unnamed: R101.P$1 (1), U101.69 (PA10)
OTG_FS_DM: U101.70 (PA11); also elsewhere on the board
OTG_FS_DP: U101.71 (PA12); also elsewhere on the board
PB2-BOOT1: R102.P$1 (1), U101.37 (PB2)
PRESSURE_SENS: U101.34 (PC5); also elsewhere on the board
SDIO_CK: U101.80 (PC12); also elsewhere on the board
SDIO_CMD: U101.83 (PD2); also elsewhere on the board
SDIO_D0: U101.65 (PC8); also elsewhere on the board
SDIO_D1: U101.66 (PC9); also elsewhere on the board
SDIO_D2: U101.78 (PC10); also elsewhere on the board
SDIO_D3: U101.79 (PC11); also elsewhere on the board
SERIAL_FMU_TO_IO: U101.63 (PC6); also elsewhere on the board
SERIAL_IO_TO_FMU: U101.64 (PC7); also elsewhere on the board
SPI_EXT_MISO: U101.4 (PE5); also elsewhere on the board
SPI_EXT_MOSI: U101.5 (PE6); also elsewhere on the board
SPI_EXT_SCK: U101.1 (PE2); also elsewhere on the board
SPI_INT_MISO: U101.31 (PA6); also elsewhere on the board
SPI_INT_MOSI: U101.32 (PA7); also elsewhere on the board
SPI_INT_SCK: U101.30 (PA5); also elsewhere on the board
VBUS: U101.68 (PA9); also elsewhere on the board
VDD_3V3_SENSORS_EN: U101.2 (PE3); also elsewhere on the board
VDD_5V_SENS: U101.29 (PA4); also elsewhere on the board

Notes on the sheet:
FMU SoC Ports FRAM
Note: MAG/ACCEL/GYRO_DRDY pins chosen for both timer capture and separate EXTI operaton. EXTI0 - TIM3_CH3 - GYRO1 EXTI1 - <free> EXTI2 - <free> EXTI3 - <free> EXTI4 - TIM3_CH1 - ACCEL EXTI5-9 - TIM3_CH2 - MAG
Timer allocation: PE9: TIM1_CH1: FMU-CH4 PE11: TIM1_CH2: FMU-CH3 PE13: TIM1_CH3: FMU-CH2 PE14: TIM1_CH4: FMU-CH1 PA15: TIM2_CH1: ALARM PB0: TIM3_CH3: GYRO1_DRDY PB1: TIM3_CH4: GYRO2_DRDY PB4: TIM3_CH1: ACCEL_DRDY PB5: TIM3_CH2: MAG_DRDY PD13: TIM4_CH2: FMU-CH5 PD14: TIM4_CH3: FMU-CH6 PD15: TIM4_CH4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
IO debug console
Spare ADC
ALL SHEETS SAME REVISION

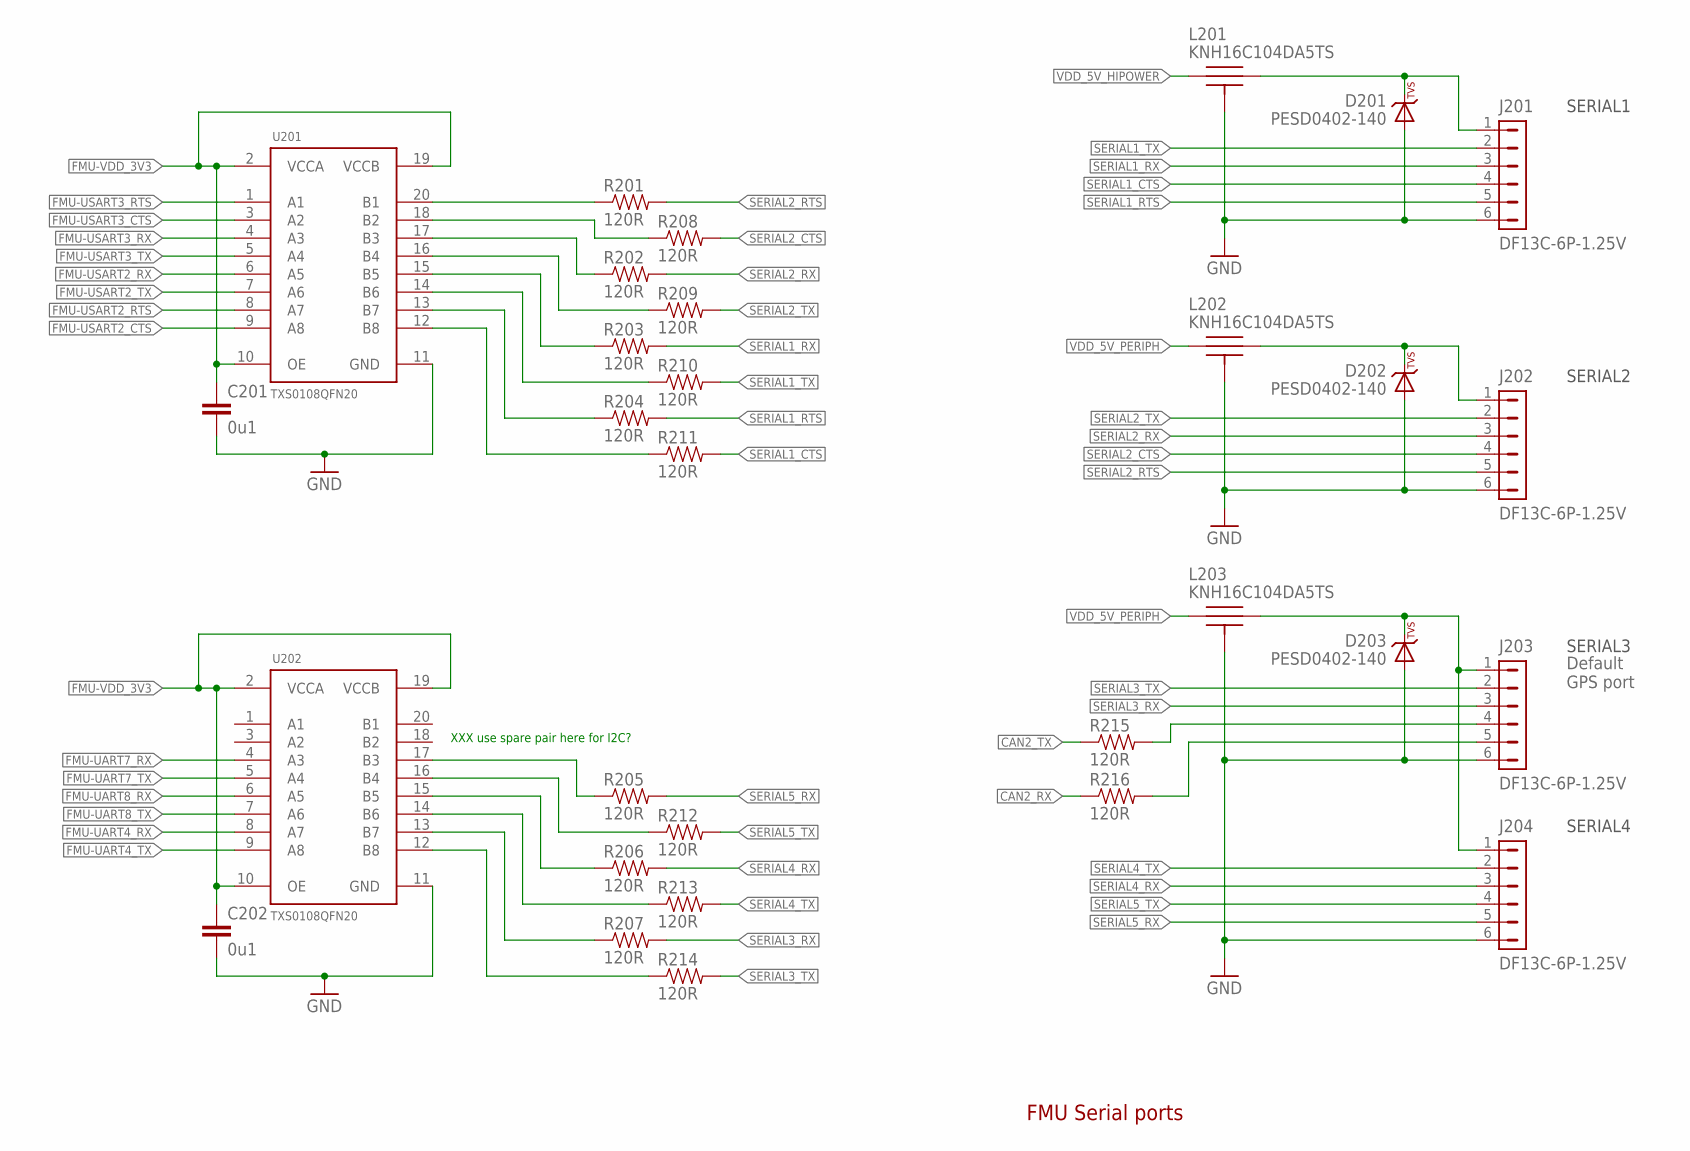
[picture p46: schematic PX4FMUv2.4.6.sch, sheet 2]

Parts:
C201, C202: 0u1; 0402-CAP; PARTNO CC0402ZRY5V7BB104
D201, D202, D203: PESD0402-140; 0402-TVS; PARTNO PESD0402-140
J201, J202, J203, J204: DF13C-6P-1.25V; PARTNO DF13C-6P-1.25V(20)
L201, L202, L203: KNH16C104DA5TS; KYOCERA-KNH16-DA; PARTNO KNH16C104DA5TS
R201, R202, R203, R204, R205, R206, R207, R208, R209, R210, R211, R212, R213, R214, R215, R216: 120R; 0402-RES; PARTNO RC0402FR-07120RL
U201, U202: TXS0108QFN20; QFN20-RGY; PARTNO TXS0108ERGYR

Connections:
CAN2_RX: R216.P$1 (1); also elsewhere on the board
CAN2_TX: R215.P$1 (1); also elsewhere on the board
FMU-UART4_RX: U202.8 (A7); also elsewhere on the board
FMU-UART4_TX: U202.9 (A8); also elsewhere on the board
FMU-UART7_RX: U202.4 (A3); also elsewhere on the board
FMU-UART7_TX: U202.5 (A4); also elsewhere on the board
FMU-UART8_RX: U202.6 (A5); also elsewhere on the board
FMU-UART8_TX: U202.7 (A6); also elsewhere on the board
FMU-USART2_CTS: U201.9 (A8); also elsewhere on the board
FMU-USART2_RTS: U201.8 (A7); also elsewhere on the board
FMU-USART2_RX: U201.6 (A5); also elsewhere on the board
FMU-USART2_TX: U201.7 (A6); also elsewhere on the board
FMU-USART3_CTS: U201.3 (A2); also elsewhere on the board
FMU-USART3_RTS: U201.1 (A1); also elsewhere on the board
FMU-USART3_RX: U201.4 (A3); also elsewhere on the board
FMU-USART3_TX: U201.5 (A4); also elsewhere on the board
FMU-VDD_3V3: C201.P$1 (1), C202.P$1 (1), U201.2 (VCCA), U201.10 (OE), U201.19 (VCCB), U202.2 (VCCA), U202.10 (OE), U202.19 (VCCB); also elsewhere on the board
GND: C201.P$2 (2), C202.P$2 (2), D201.A, D202.A, D203.A, J201.6, J202.6, J203.6, J204.6, L201.P$3, L201.P$4, L201.P$5, L202.P$3, L202.P$4, L202.P$5, L203.P$3, L203.P$4, L203.P$5, U201.11 (GND), U202.11 (GND); also elsewhere on the board
unnamed: D201.C, J201.1, L201.P$2
unnamed: J203.4, R215.P$2 (2)
unnamed: J203.5, R216.P$2 (2)
unnamed: R201.P$1 (1), U201.20 (B1)
unnamed: R208.P$1 (1), U201.18 (B2)
unnamed: R202.P$1 (1), U201.17 (B3)
unnamed: R209.P$1 (1), U201.16 (B4)
unnamed: R203.P$1 (1), U201.15 (B5)
unnamed: R210.P$1 (1), U201.14 (B6)
unnamed: R204.P$1 (1), U201.13 (B7)
unnamed: R211.P$1 (1), U201.12 (B8)
unnamed: R207.P$1 (1), U202.13 (B7)
unnamed: R214.P$1 (1), U202.12 (B8)
unnamed: R205.P$1 (1), U202.17 (B3)
unnamed: R212.P$1 (1), U202.16 (B4)
unnamed: R206.P$1 (1), U202.15 (B5)
unnamed: R213.P$1 (1), U202.14 (B6)
unnamed: D203.C, J203.1, J204.1, L203.P$2
unnamed: D202.C, J202.1, L202.P$2
SERIAL1_CTS: J201.4, R211.P$2 (2)
SERIAL1_RTS: J201.5, R204.P$2 (2)
SERIAL1_RX: J201.3, R203.P$2 (2); also elsewhere on the board
SERIAL1_TX: J201.2, R210.P$2 (2); also elsewhere on the board
SERIAL2_CTS: J202.4, R208.P$2 (2)
SERIAL2_RTS: J202.5, R201.P$2 (2)
SERIAL2_RX: J202.3, R202.P$2 (2); also elsewhere on the board
SERIAL2_TX: J202.2, R209.P$2 (2); also elsewhere on the board
SERIAL3_RX: J203.3, R207.P$2 (2); also elsewhere on the board
SERIAL3_TX: J203.2, R214.P$2 (2); also elsewhere on the board
SERIAL4_RX: J204.3, R206.P$2 (2); also elsewhere on the board
SERIAL4_TX: J204.2, R213.P$2 (2); also elsewhere on the board
SERIAL5_RX: J204.5, R205.P$2 (2); also elsewhere on the board
SERIAL5_TX: J204.4, R212.P$2 (2); also elsewhere on the board
VDD_5V_HIPOWER: L201.P$1; also elsewhere on the board
VDD_5V_PERIPH: L202.P$1, L203.P$1; also elsewhere on the board

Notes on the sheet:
FMU Serial ports
XXX use spare pair here for I2C?
SERIAL2
SERIAL1
SERIAL3
SERIAL4
Default GPS port

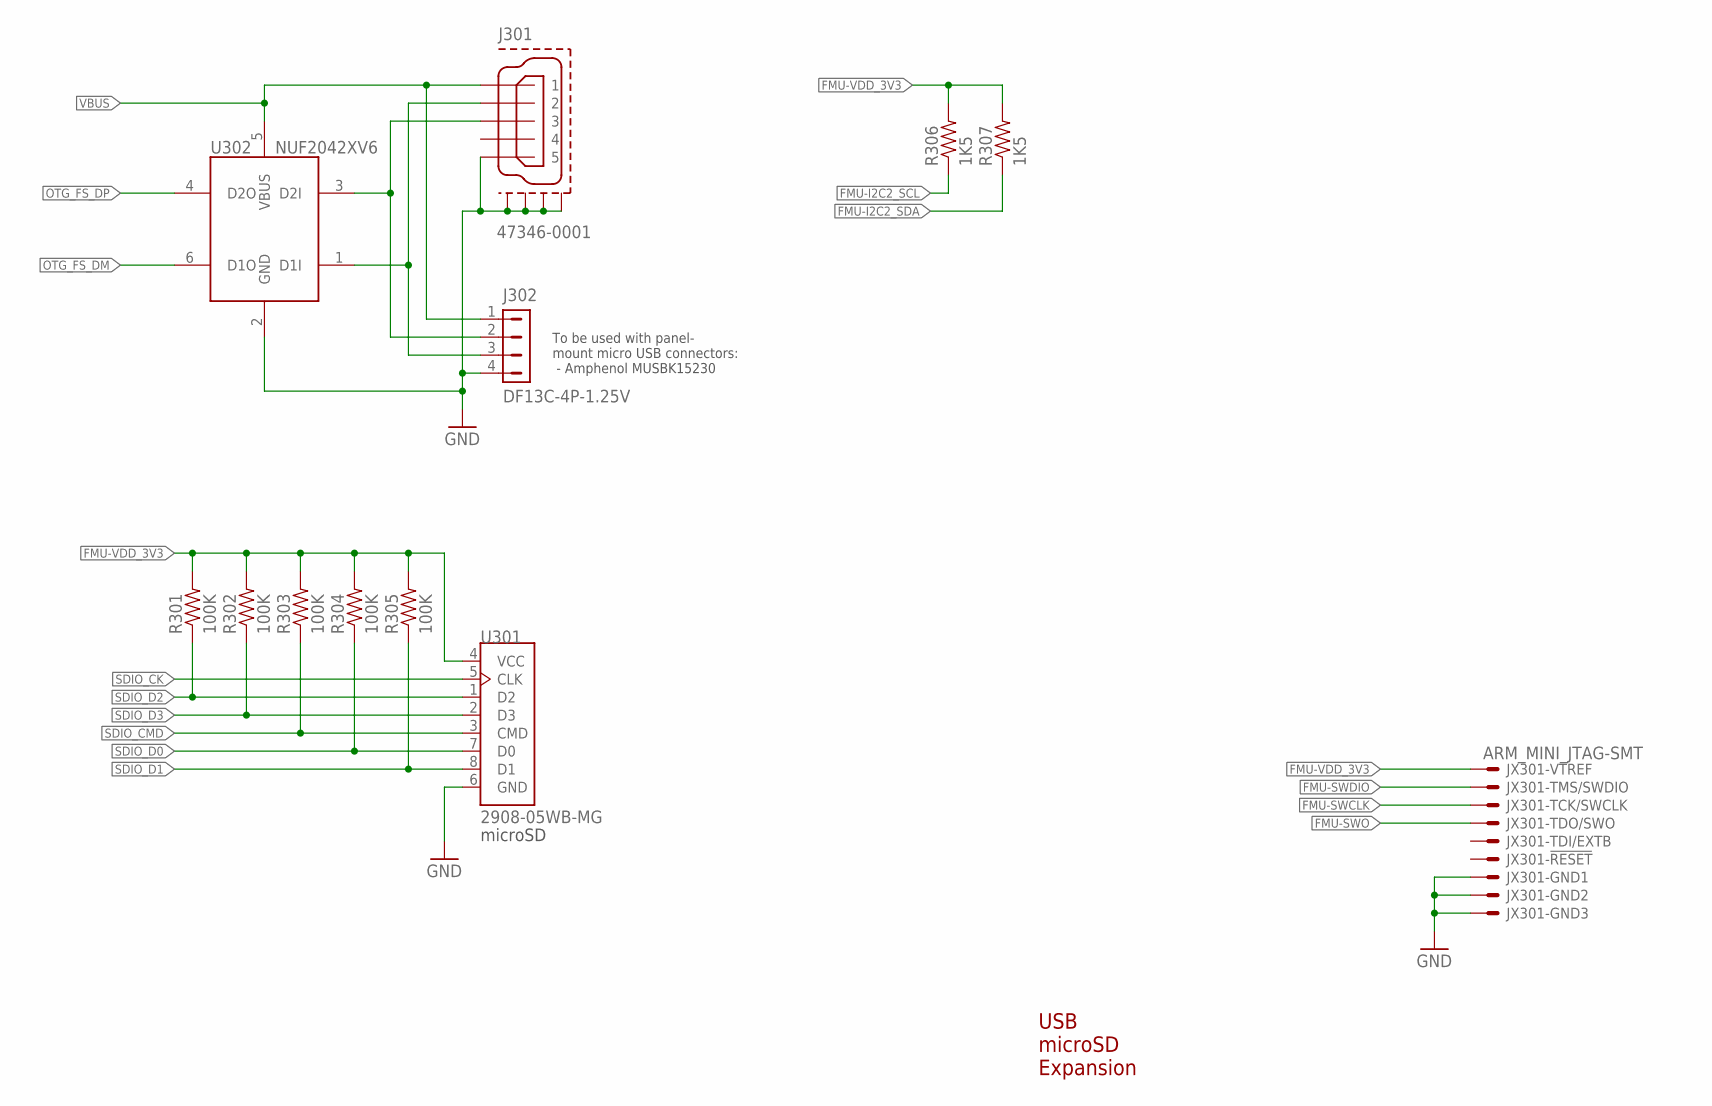
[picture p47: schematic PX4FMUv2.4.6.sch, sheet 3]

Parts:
J301: 47346-0001; MOLEX-47346-0001; PARTNO 47346-0001
J302: DF13C-4P-1.25V; PARTNO DF13C-4P-1.25V(20)
JX301: ARM_MINI_JTAG-SMT; FTSH-105-01-XXX-DV-K; PARTNO M50-3900542
R301, R302, R303, R304, R305: 100K; 0402-RES; PARTNO RC0402FR-07100KL
R306, R307: 1K5; 0402-RES; PARTNO RC0402FR-071K5L
U301: 2908-05WB-MG; MICROSD; PARTNO 2908-05WB-MG
U302: NUF2042XV6; SOT563-6; PARTNO NUF2042XV6T1G

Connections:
FMU-I2C2_SCL: R306.P$1 (1); also elsewhere on the board
FMU-I2C2_SDA: R307.P$1 (1); also elsewhere on the board
FMU-SWCLK: JX301.4; also elsewhere on the board
FMU-SWDIO: JX301.2; also elsewhere on the board
FMU-SWO: JX301.6; also elsewhere on the board
FMU-VDD_3V3: JX301.1, R301.P$2 (2), R302.P$2 (2), R303.P$2 (2), R304.P$2 (2), R305.P$2 (2), R306.P$2 (2), R307.P$2 (2), U301.4 (VCC); also elsewhere on the board
GND: J301.GND (5), J301.GND1, J301.GND2, J301.GND3, J301.GND4, J302.4, JX301.3, JX301.5, JX301.9, U301.6 (GND), U302.2 (GND); also elsewhere on the board
OTG_DM1: J301.D- (2), J302.3, U302.1 (D1I)
OTG_DP1: J301.D+ (3), J302.2, U302.3 (D2I)
OTG_FS_DM: U302.6 (D1O); also elsewhere on the board
OTG_FS_DP: U302.4 (D2O); also elsewhere on the board
SDIO_CK: U301.5 (CLK); also elsewhere on the board
SDIO_CMD: R303.P$1 (1), U301.3 (CMD); also elsewhere on the board
SDIO_D0: R304.P$1 (1), U301.7 (D0); also elsewhere on the board
SDIO_D1: R305.P$1 (1), U301.8 (D1); also elsewhere on the board
SDIO_D2: R301.P$1 (1), U301.1 (D2); also elsewhere on the board
SDIO_D3: R302.P$1 (1), U301.2 (D3); also elsewhere on the board
VBUS: J301.VBUS (1), J302.1, U302.5 (VBUS); also elsewhere on the board

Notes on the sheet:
USB microSD Expansion
microSD
To be used with panel- mount micro USB connectors: - Amphenol MUSBK15230

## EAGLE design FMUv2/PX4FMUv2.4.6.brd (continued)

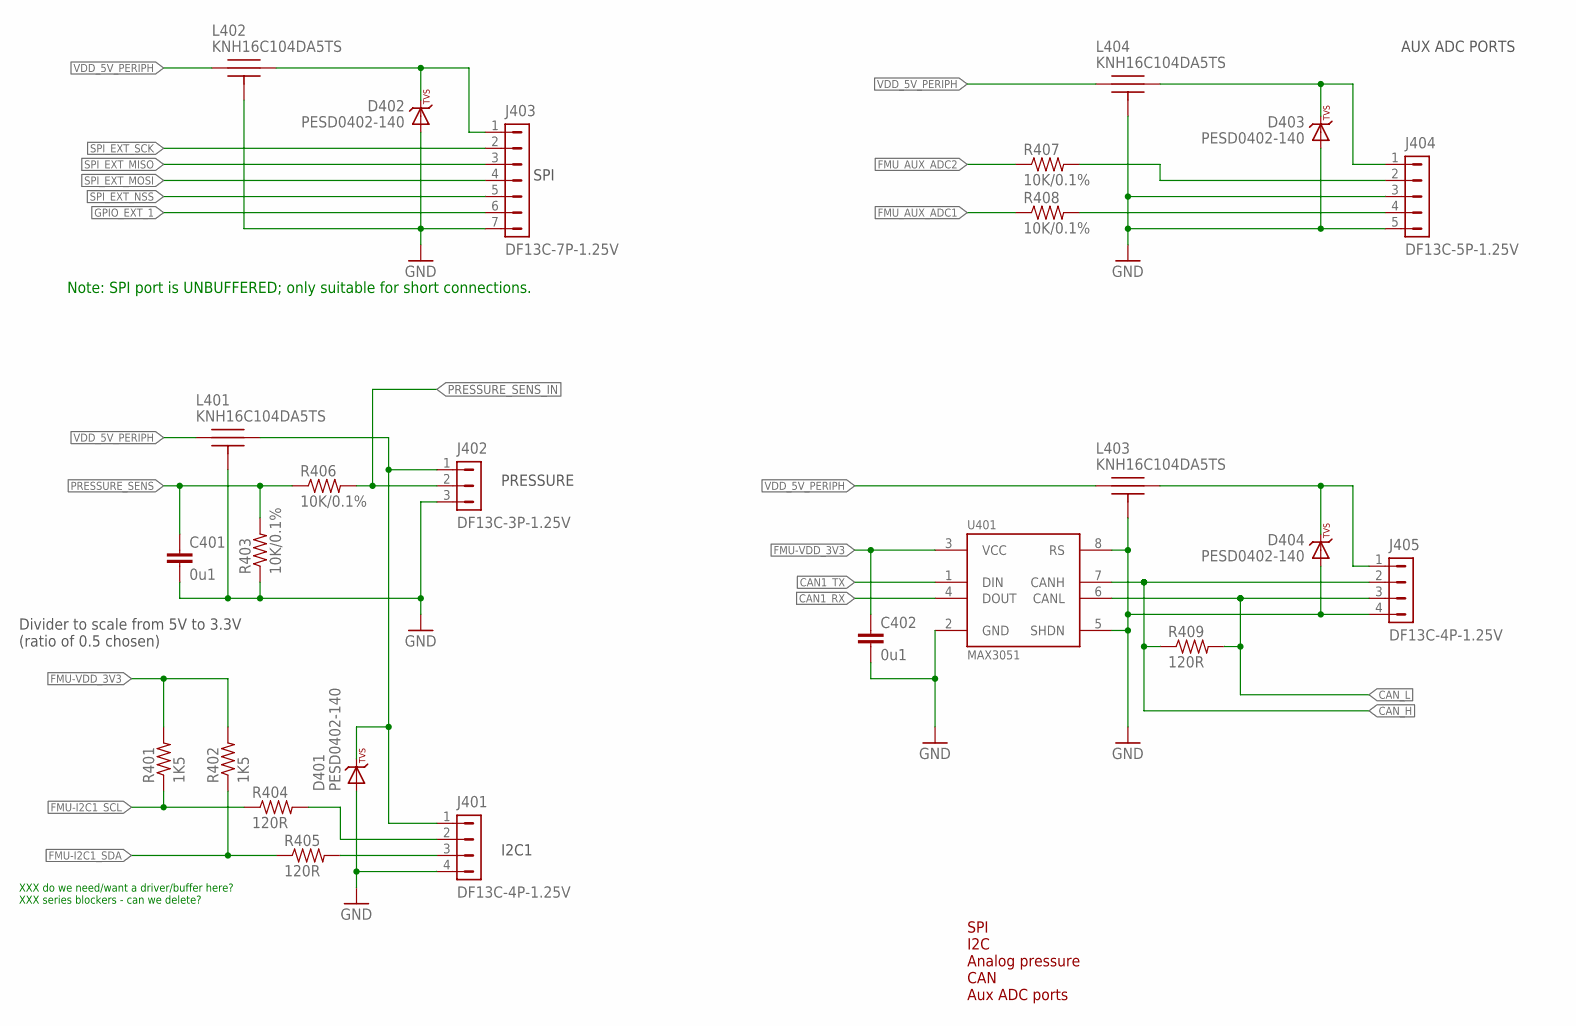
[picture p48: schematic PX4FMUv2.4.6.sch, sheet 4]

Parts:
C401, C402: 0u1; 0402-CAP; PARTNO CC0402ZRY5V7BB104
D401, D402, D403, D404: PESD0402-140; 0402-TVS; PARTNO PESD0402-140
J401, J405: DF13C-4P-1.25V; PARTNO DF13C-4P-1.25V(20)
J402: DF13C-3P-1.25V; PARTNO DF13C-3P-1.25V(20)
J403: DF13C-7P-1.25V; PARTNO DF13C-7P-1.25V(20)
J404: DF13C-5P-1.25V; PARTNO DF13C-5P-1.25V(20)
L401, L402, L403, L404: KNH16C104DA5TS; KYOCERA-KNH16-DA; PARTNO KNH16C104DA5TS
R401, R402: 1K5; 0402-RES; PARTNO RC0402FR-071K5L
R403, R406, R407, R408: 10K/0.1%; 0402-RES; PARTNO ERA-2AEB103X
R404, R405, R409: 120R; 0402-RES; PARTNO RC0402FR-07120RL
U401: MAX3051; SOT23-8; PARTNO MAX3051EKA

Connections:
!SPI_EXT_NSS: J403.5; also elsewhere on the board
CAN1_RX: U401.4 (DOUT); also elsewhere on the board
CAN1_TX: U401.1 (DIN); also elsewhere on the board
CAN_H: J405.2, R409.P$1 (1), U401.7 (CANH); also elsewhere on the board
CAN_L: J405.3, R409.P$2 (2), U401.6 (CANL); also elsewhere on the board
FMU-I2C1_SCL: R401.P$1 (1), R404.P$1 (1); also elsewhere on the board
FMU-I2C1_SDA: R402.P$1 (1), R405.P$1 (1); also elsewhere on the board
FMU-VDD_3V3: C402.P$1 (1), R401.P$2 (2), R402.P$2 (2), U401.3 (VCC); also elsewhere on the board
FMU_AUX_ADC1: R408.P$1 (1); also elsewhere on the board
FMU_AUX_ADC1_PROT: J404.4, R408.P$2 (2)
FMU_AUX_ADC2: R407.P$1 (1); also elsewhere on the board
FMU_AUX_ADC2_PROT: J404.2, R407.P$2 (2)
GND: C401.P$2 (2), C402.P$2 (2), D401.A, D402.A, D403.A, D404.A, J401.4, J402.3, J403.7, J404.3, J404.5, J405.4, L401.P$3, L401.P$4, L401.P$5, L402.P$3, L402.P$4, L402.P$5, L403.P$3, L403.P$4, L403.P$5, L404.P$3, L404.P$4, L404.P$5, R403.P$1 (1), U401.2 (GND), U401.5 (SHDN), U401.8 (RS); also elsewhere on the board
GPIO_EXT_1: J403.6; also elsewhere on the board
unnamed: J401.2, R404.P$2 (2)
unnamed: J401.3, R405.P$2 (2)
unnamed: D402.C, J403.1, L402.P$2
unnamed: D401.C, J401.1, J402.1, L401.P$2
unnamed: D404.C, J405.1, L403.P$2
unnamed: D403.C, J404.1, L404.P$2
PRESSURE_SENS: C401.P$1 (1), R403.P$2 (2), R406.P$1 (1); also elsewhere on the board
PRESSURE_SENS_IN: J402.2, R406.P$2 (2); also elsewhere on the board
SPI_EXT_MISO: J403.3; also elsewhere on the board
SPI_EXT_MOSI: J403.4; also elsewhere on the board
SPI_EXT_SCK: J403.2; also elsewhere on the board
VDD_5V_PERIPH: L401.P$1, L402.P$1, L403.P$1, L404.P$1; also elsewhere on the board

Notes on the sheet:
SPI
PRESSURE
XXX do we need/want a driver/buffer here? XXX series blockers - can we delete?
I2C1
AUX ADC PORTS
SPI I2C Analog pressure CAN Aux ADC ports
Note: SPI port is UNBUFFERED; only suitable for short connections.
Divider to scale from 5V to 3.3V (ratio of 0.5 chosen)


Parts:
C501, C506, C509, C511: 10u/10V; 0805-CAP; PARTNO CC0805ZKY5V6BB106
C502, C503, C507, C508, C514: 0u1; 0402-CAP; PARTNO CC0402ZRY5V7BB104
C504, C505: 10n; 0402-CAP; PARTNO CC0402KRX7R7BB103
C510: 0u47; 0402-CAP; PARTNO C1005X5R1C474K050BC
C512, C513: 2u2; 0603-CAP; PARTNO C1608X6S1C225K080AC
C515: 0u01; 0603-CAP; PARTNO 06033C103JAT2A
U501: L3GD20; L3G4200DH-MAN; PARTNO L3GD20
U502: L3GD20H; LGA-16L; PARTNO L3GD20H
U504: LSM303D; LGA-16L; PARTNO LSM303D
U505: MPU-6000; QFN-24; PARTNO MPU-6000
U506: MS5611-01BA; PARTNO MS5611-01BA
X503: 0512811094; 51281-1094; PARTNO 0781191109

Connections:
!ACCEL_MAG_CS: U504.8 (CS), X503.6; also elsewhere on the board
!BARO_CS: U506.5 (CSB2); also elsewhere on the board
!GYRO_CS: U501.5 (CS), U502.5 (CS), X503.7; also elsewhere on the board
!MPU_CS: U505.8 (/CS); also elsewhere on the board
ACCEL_DRDY: U504.11 (INT1), X503.3; also elsewhere on the board
GND: C501.P$2 (2), C502.P$2 (2), C503.P$2 (2), C504.P$2 (2), C505.P$2 (2), C506.P$2 (2), C507.P$2 (2), C508.P$2 (2), C509.P$2 (2), C511.P$2 (2), C512.P$2 (2), C513.P$2 (2), C514.P$2 (2), C515.P$2 (2), U501.8 (RES_P8_GND), U501.9 (RES_P9_GND), U501.10 (RES_P10_GND), U501.11 (RES_P11_GND), U501.12 (RES_P12_GND), U501.13 (GND), U502.9 (GND), U502.10 (GND), U502.11 (GND), U502.12 (GND), U502.13 (GND), U504.5 (GND), U504.10 (RSRV), U504.12 (GND), U504.13 (GND), U504.16 (GND), U505.1 (CLKIN), U505.18 (GND), U506.2 (PS), U506.3 (GND), X503.2; also elsewhere on the board
GYRO_DRDY: U501.6 (DRDY/INT2), U502.6 (DRDY/INT2), X503.5; also elsewhere on the board
MAG_DRDY: U504.9 (INT2), X503.4; also elsewhere on the board
MPU_DRDY: U505.12 (INT); also elsewhere on the board
unnamed: C509.P$1 (1), U504.15 (C1)
unnamed: C510.P$1 (1), U504.2 (SETC)
unnamed: C510.P$2 (2), U504.3 (SETP)
unnamed: C505.P$1 (1), U502.14 (CAP)
unnamed: C504.P$1 (1), U501.14 (PLLFILT)
unnamed: C512.P$1 (1), U505.10 (REGOUT)
unnamed: C515.P$1 (1), U505.20 (CPOUT)
SPI_INT_MISO: U501.4 (SDO/SA0), U502.4 (SDO/SA0), U504.7 (SDO/SA0), U505.9 (AD0/SDO), U506.6 (SDO), X503.9; also elsewhere on the board
SPI_INT_MOSI: U501.3 (SDA/SDI/SDO), U502.3 (SDA/SDI/SDO), U504.6 (SDA/SDI/SDO), U505.24 (SDA/SDI), U506.7 (SDI/SDA), X503.8; also elsewhere on the board
SPI_INT_SCK: U501.2 (SCL/SPC), U502.2 (SCL/SPC), U504.4 (SCL/SPC), U505.23 (SCL/SCLK), U506.8 (SCLK), X503.10; also elsewhere on the board
VDD_3V3_SENSORS: C501.P$1 (1), C502.P$1 (1), C503.P$1 (1), C506.P$1 (1), C507.P$1 (1), C508.P$1 (1), C511.P$1 (1), C513.P$1 (1), C514.P$1 (1), U501.1 (VDD_IO), U501.15 (RES_P15_VDD), U501.16 (VDD), U502.1 (VDD_IO), U502.15 (VDD), U502.16 (VDD), U504.1 (VDD_IO), U504.14 (VDD), U505.13 (VDD), U506.1 (VDD), X503.1; also elsewhere on the board

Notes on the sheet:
Sensors
Switch to L3GD20H once available (Q3/2013) WARNING: DIFFERENT HW, SW COMPATIBLE
NOTE: place 10uF cap close to gyros
Stuff option 1: L3GD20 (legacy gyro)
Stuff option 2: L3GD20H (replacement gyro)
Stuff option 4: onboard accel/mag
Valid stuff option combos: 1 + 4 + 5 2 + 4 + 5 3 + 5 ONLY DO NOT stuff 1 + 2 at the same time DO NOT stuff 3 with any of 1, 2 or 4
Stuff option 5: MPU6000
Stuff option 3: offboard gyro/accel/mag
STUFF C503 WITH 220R RESISTOR


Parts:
B601: MS621FE; PARTNO MS621FE-FL11E
C601: 10u/25V; 0805-CAP; PARTNO CL21A106KAYNNNE
C602: 10n; 0402-CAP; PARTNO CC0402KRX7R7BB103
C603: 1u; 0603-CAP; PARTNO CC0603ZRY5V7BB105
C604, C605: 22u/25V; 0805-CAP; PARTNO CL21A226MAQNNNE
C606, C607, C608, C609, C610, C612, C615, C616, C617: 0u1; 0402-CAP; PARTNO CC0402ZRY5V7BB104
C611, C613: 2u2; 0603-CAP; PARTNO C1608X6S1C225K080AC
C614, C618: 100u; 1206-CAP; PARTNO C3216X5R1A107M160AC
D602: RB751V40T1G; SOD323; PARTNO RB751V40T1G
L603: KNH16C104DA5TS; KYOCERA-KNH16-DA; PARTNO KNH16C104DA5TS
R602, R604: 1M; 0402-RES; PARTNO RC0402FR-071ML
R603, R611, R615, R635: 10K; 0402-RES; PARTNO RC0402FR-0710KL
R608: 1K; 0402-RES; PARTNO RC0402FR-071KL
R609, R610: 10K/0.1%; 0402-RES; PARTNO ERA-2AEB103X
R616: 25K5; 0402-RES; PARTNO RMCF0402FT25K5
R617: 16K5; 0402-RES; PARTNO RMCF0402FT16K5
R621: 220R; 0603-RES; PARTNO RC1608J100CS
S601: RESET; EVQP7J01K; PARTNO EVQ-P7J01P
U101: STM32F4X7VX; TQFP100; PARTNO STM32F427VI
U601, U602: BQ24315; QFN8-DSG; PARTNO BQ24315DSGR
U603: MIC5332; MLF-8-EPAD; PARTNO MIC5332-SSYMT

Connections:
!VDD_5V_HIPOWER_OC: R602.P$1 (1), U601.4 (!FAULT); also elsewhere on the board
!VDD_5V_PERIPH_EN: R615.P$1 (1), U601.5 (!CE), U602.5 (!CE); also elsewhere on the board
!VDD_5V_PERIPH_OC: R604.P$1 (1), U602.4 (!FAULT); also elsewhere on the board
FMU-!RESET: C609.P$2 (2), R635.P$1 (1), S601.A1 (1), U101.14 (NRST), U603.3 (POR2); also elsewhere on the board
FMU-BOOT0: R611.P$2 (2), U101.94 (BOOT0); also elsewhere on the board
FMU-VDD_3V3: C603.P$1 (1), C604.P$1 (1), C606.P$1 (1), C607.P$1 (1), C608.P$1 (1), C610.P$1 (1), C612.P$1 (1), C616.P$1 (1), D602.A, R602.P$2 (2), R604.P$2 (2), U101.11 (VDD), U101.19 (VDD), U101.21 (VREF+), U101.22 (VDDA), U101.28 (VDD), U101.50 (VDD), U101.75 (VDD), U101.100 (VDD), U603.7 (VOUT2); also elsewhere on the board
FMU-VDD_5V5: C601.P$1 (1), C615.P$1 (1), L603.P$2, R603.P$1 (1), U603.1 (VIN), U603.4 (EN2)
GND: B601.2 (NEG), C601.P$2 (2), C602.P$1 (1), C603.P$2 (2), C604.P$2 (2), C605.P$2 (2), C606.P$2 (2), C607.P$2 (2), C608.P$2 (2), C609.P$1 (1), C610.P$2 (2), C611.P$2 (2), C612.P$2 (2), C613.P$2 (2), C614.P$2 (2), C615.P$2 (2), C616.P$2 (2), C617.P$2 (2), C618.P$2 (2), L603.P$3, L603.P$4, L603.P$5, R610.P$2 (2), R611.P$1 (1), R615.P$2 (2), R616.P$2 (2), R617.P$2 (2), R621.1, S601.B3 (2), U101.10 (VSS), U101.20 (VSSA), U101.27 (VSS), U101.74 (VSS), U101.99 (VSS), U601.2 (VSS), U601.6 (VBAT), U601.GND (VSS), U601.P$2 (VSS), U601.P$3 (VSS), U602.2 (VSS), U602.6 (VBAT), U602.GND (VSS), U602.P$2 (VSS), U602.P$3 (VSS), U603.2 (GND), U603.GND; also elsewhere on the board
unnamed: C613.P$1 (1), U101.73 (VCAP_2)
unnamed: C602.P$2 (2), U603.6 (CSET)
unnamed: C611.P$1 (1), U101.49 (VCAP_1)
unnamed: D602.C, R608.P$2 (2)
unnamed: R616.P$1 (1), U602.7 (ILIM)
unnamed: R617.P$1 (1), U601.7 (ILIM)
VBAT: B601.1 (POS), R608.P$1 (1), U101.6 (VBAT); also elsewhere on the board
VDD_3V3_SENSORS: C605.P$1 (1), C617.P$1 (1), R621.2, U603.8 (VOUT1); also elsewhere on the board
VDD_3V3_SENSORS_EN: R603.P$2 (2), R635.P$2 (2), U603.5 (EN1); also elsewhere on the board
VDD_5V_HIPOWER: C614.P$1 (1), U601.8 (OUT); also elsewhere on the board
VDD_5V_IN: L603.P$1, R609.P$2 (2), U601.1 (IN), U602.1 (IN); also elsewhere on the board
VDD_5V_PERIPH: C618.P$1 (1), U602.8 (OUT); also elsewhere on the board
VDD_5V_SENS: R609.P$1 (1), R610.P$1 (1); also elsewhere on the board

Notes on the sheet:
FMU Power and Reset
Bypass caps as close to device pins as possible.
Note: Maximise copper area connected to center ground pad.
POR reset delay 1s / uF
Current Limits: I(limit) = 25000 / R(ilim) 25K = 1A, 16K5 = 1.5A
Drain resistor for Sensor Power Rail
Note: Do not populate R603 and R635. Only one may be populated at a time.
Note: Do not populate R635.


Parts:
C701: 0u1; 0402-CAP; PARTNO CC0402ZRY5V7BB104
C702: 1u; 0603-CAP; PARTNO CC0603ZRY5V7BB105
C703: 5n6; 0402-CAP; PARTNO C0402C562K5RACTU
C704: 0u47; 0402-CAP; PARTNO C1005X5R1C474K050BC
D701: PESD0402-140; 0402-TVS; PARTNO PESD0402-140
J701: DF13C-2P-1.25V; PARTNO DF13C-2P-1.25V(20)
J702: DF13C-3P-1.25V; PARTNO DF13C-3P-1.25V(20)
L701: 47uH; 0805-IND; PARTNO MLZ2012M470W
LED701, LED703: AMBER; 0603-LED; PARTNO APTD1608SECK
LED702, LED704: GREEN; 0603-LED; PARTNO APTD1608CGCK
LED705: BLUE; 0603-LED; PARTNO APTD1608QBC/D
R701: 9K09; 0402-RES; PARTNO RMCF0402FT9K09
R702, R704: 10K; 0402-RES; PARTNO RC0402FR-0710KL
R703: 100K; 0402-RES; PARTNO RC0402FR-07100KL
R705: 453K; 0402-RES; PARTNO RMCF0402FT453K
R706: 16K5; 0402-RES; PARTNO RMCF0402FT16K5
R707, R708, R709, R711, R712, R735, R736: 220R; 0402-RES; PARTNO RC0402FR-07220RL
R710: 68R; 0402-RES; PARTNO ERJ-2GEJ680X
R713: 1K5; 0402-RES; PARTNO RC0402FR-071K5L
U701: TCA62724FMG; SON10; PARTNO TCA62724FMG
U702: LT3469; SOT23-8; PARTNO LT3469ETS8
U703: LRTB GFTG-T7AW-1+V7A7-29+R5T9-49-L; 6-PLCC; PARTNO LRTB GFTG-T7AW-1+V7A7-29+R5T9-49-L

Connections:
!FMU-LED_AMBER: R707.P$1 (1); also elsewhere on the board
!IO-LED_AMBER: R709.P$1 (1); also elsewhere on the board
!IO-LED_BLUE: R712.P$1 (1); also elsewhere on the board
!IO-LED_SAFETY: R710.P$2 (2); also elsewhere on the board
ALARM: R701.P$2 (2); also elsewhere on the board
FMU-!RESET: U701.4 (!RESET); also elsewhere on the board
FMU-I2C2_SCL: U701.3 (SCL); also elsewhere on the board
FMU-I2C2_SDA: U701.2 (SDA); also elsewhere on the board
FMU-VDD_3V3: C701.P$1 (1), U701.1 (!SHDN), U701.10 (VIN); also elsewhere on the board
GND: C701.P$2 (2), C702.P$2 (2), C703.P$2 (2), C704.P$2 (2), D701.A, J701.2, R702.P$2 (2), R704.P$1 (1), R706.P$2 (2), R708.P$1 (1), R711.P$1 (1), R713.P$2 (2), U701.5 (GND), U702.4 (GND); also elsewhere on the board
IO-VDD_3V3: D701.C, J702.1; also elsewhere on the board
IO-VDD_5V5: LED702.A, LED703.A, LED705.A; also elsewhere on the board
unnamed: LED704.C, R711.P$2 (2)
unnamed: LED705.C, R712.P$2 (2)
unnamed: R707.P$2 (2), R735.P$1 (1)
unnamed: R705.P$2 (2), R706.P$1 (1), U702.2 (FB)
unnamed: R702.P$1 (1), R703.P$2 (2), U702.8 (-IN)
unnamed: LED701.C, R735.P$2 (2)
unnamed: C703.P$1 (1), J701.1, R703.P$1 (1), U702.1 (OUT)
unnamed: R701.P$1 (1), U702.7 (+IN)
unnamed: LED702.C, R708.P$2 (2)
unnamed: L701.P$2 (2), U702.5 (SW)
unnamed: C704.P$1 (1), R705.P$1 (1), U702.6 (VCC)
unnamed: R709.P$2 (2), R736.P$1 (1)
unnamed: LED703.C, R736.P$2 (2)
unnamed: J702.2, R710.P$1 (1)
unnamed: R704.P$2 (2), U701.6 (REXT)
RGB_LED_3: U701.9 (OUT0), U703.C1 (C)
RGB_LED_4: U701.8 (OUT1), U703.C2 (C)
RGB_LED_14: U701.7 (OUT2), U703.C3 (C)
SAFETY: J702.3, R713.P$1 (1); also elsewhere on the board
VDD_5V_IN: C702.P$1 (1), L701.P$1 (1), LED701.A, LED704.A, U702.3 (VIN), U703.A1 (A), U703.A2 (A), U703.A3 (A); also elsewhere on the board

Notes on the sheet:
LEDs Piezo driver Safety switch
Switch: E-Switch LP1OA1AR
SAFETY
LED should be Omron LRTBG6SG-U4AA-1+V2B4-25+S or similar 6PLCC high-brigtness type.
Iout = (1.17 / REXT) * 460 10K = 54mA, selected for maximum daylight visibility.
Note: LED driver is on FMU-I2C2 so that an external instance can be connected to FMU-I2C1.
All LEDs nominal target 60mcd for good daylight visibility. Resistor values have been adjusted to optimize BOM. Green: APG1608CGKC/T Vf(typ): 2.1V Target If: 20mA Selected R: 220 Cacluated If @ 5.5V: 15mA Amber: APT1608SECK Vf(typ): 2.1V Target If: 5mA Selected R: 440 Cacluated If @ 5.5V: 8mA Blue: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
Component values taken directly from the LTC evaluation design. Note that the ALARM input should idle low to minimise power dissipation.


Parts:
C801, C802, C803, C804: 0u1; 0402-CAP; PARTNO CC0402ZRY5V7BB104
C805, C806: 8p; 0402-CAP; PARTNO C1005C0G1H080C
D801: PESD0402-140; 0402-TVS; PARTNO PESD0402-140
J801: JST-ZH-3; JST-ZH-SMT-VERTICAL; PARTNO B3B-ZR-SM4-TF (LF)(SN)(P)
JX801: HEADER-3X1BOARDEDGE-SHORT; HEADER_3X01_SMD_H_BOARD_EDGE_SHORT
JX802: ARM_MINI_JTAG-SMT; FTSH-105-01-XXX-DV-K; PARTNO M50-3900542
R801, R802: 10K; 0402-RES; PARTNO RC0402FR-0710KL
R803, R804: 220R; 0402-RES; PARTNO RC0402FR-07220RL
S801: RESET; EVQP7J01K; PARTNO EVQ-P7J01P
U801: STM32F10XCXT6; TQFP48; PARTNO STM32F100C8T6B
X801: 3.2x2.5 mm / 24 MHz / 15 ppm; OSCILLATOR-3.2X2.5; PARTNO NX3225SA-24.000000MHZ

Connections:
!IO-LED_AMBER: U801.28 (PB15); also elsewhere on the board
!IO-LED_BLUE: U801.27 (PB14); also elsewhere on the board
!IO-LED_SAFETY: U801.26 (PB13); also elsewhere on the board
!SBUS_OUTPUT_EN: U801.40 (PB4); also elsewhere on the board
GND: C801.P$1 (1), C802.P$2 (2), C803.P$2 (2), C804.P$2 (2), C805.P$2 (2), C806.P$1 (1), D801.A, J801.P$2, JX801.3 (GND), JX802.3, JX802.5, JX802.9, R801.P$2 (2), R802.P$2 (2), S801.B3 (2), U801.8 (VSSA), U801.23 (VSS_1), U801.35 (VSS_2), U801.47 (VSS_3), X801.2 (NC_2), X801.4 (NC_4); also elsewhere on the board
IO-!RESET: C801.P$2 (2), S801.A1 (1), U801.7 (NRST); also elsewhere on the board
IO-!VDD_SERVO_IN_FAULT: U801.38 (PA15); also elsewhere on the board
IO-BOOT0: R801.P$1 (1), U801.44 (BOOT0); also elsewhere on the board
IO-BOOT1: R802.P$1 (1), U801.20 (PB2)
IO-CH1: U801.10 (PA0); also elsewhere on the board
IO-CH2: U801.11 (PA1); also elsewhere on the board
IO-CH3: U801.45 (PB8); also elsewhere on the board
IO-CH4: U801.46 (PB9); also elsewhere on the board
IO-CH5: U801.16 (PA6); also elsewhere on the board
IO-CH6: U801.17 (PA7); also elsewhere on the board
IO-CH7: U801.18 (PB0); also elsewhere on the board
IO-CH8: U801.19 (PB1); also elsewhere on the board
IO-SWCLK: JX802.4, U801.37 (PA14)
IO-SWDIO: JX802.2, U801.34 (PA13)
IO-SWO: JX802.6, U801.39 (PB3)
IO-USART1_RX: J801.P$3, JX801.2 (+5V), U801.31 (PA10)
IO-USART1_TX: JX801.1 (PPM), U801.30 (PA9); also elsewhere on the board
IO-VDD_3V3: C802.P$1 (1), C803.P$1 (1), C804.P$1 (1), JX802.1, U801.9 (VDDA), U801.24 (VDD_1), U801.36 (VDD_2), U801.48 (VDD_3); also elsewhere on the board
unnamed: R803.P$1 (1), U801.12 (PA2)
unnamed: R804.P$1 (1), U801.13 (PA3)
unnamed: C806.P$2 (2), U801.6 (PD1/OSC=>), X801.1
unnamed: C805.P$1 (1), U801.5 (PD0/OSC<=), X801.3
PPM_INPUT: U801.29 (PA8); also elsewhere on the board
RSSI_IN: U801.15 (PA5), U801.33 (PA12); also elsewhere on the board
SAFETY: U801.41 (PB5); also elsewhere on the board
SBUS_INPUT: U801.22 (PB11); also elsewhere on the board
SBUS_OUTPUT: U801.21 (PB10); also elsewhere on the board
SERIAL_FMU_TO_IO: R804.P$2 (2); also elsewhere on the board
SERIAL_IO_TO_FMU: R803.P$2 (2); also elsewhere on the board
VBAT: U801.1 (VBAT); also elsewhere on the board
VDD_3V3_SPEKTRUM: D801.C, J801.P$1; also elsewhere on the board
VDD_3V3_SPEKTRUM_EN: U801.2 (PC13); also elsewhere on the board
VDD_SERVO_SENS: U801.14 (PA4); also elsewhere on the board

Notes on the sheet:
IO SoC Ports Spektrum/DSM port
LED3 moves to PB13 to make room for S.Bus output
Routed to FMU for debug purposes
IO_SERIAL1
Spektrum/DSM
Timer allocation: PA0: TIM2_CH1: IO-CH1 PA1: TIM2_CH2: IO-CH2 PB8: TIM4_CH3: IO-CH3 PB9: TIM4_CH4: IO-CH4 PA6: TIM3_CH1: IO-CH5 PA7: TIM3_CH2: IO-CH6 PB0: TIM3_CH3: IO-CH7 PB1: TIM3_CH4: IO-CH8 PA8: TIM1_CH1: PPM_IN PA11: TIM1_CH4: RSSI_IN
spare pwm
spare gpio

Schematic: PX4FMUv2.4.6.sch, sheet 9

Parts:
C901, C902, C903: 0u1; 0402-CAP; PARTNO CC0402ZRY5V7BB104
D901, D902, D903: PESD0402-140; 0402-TVS; PARTNO PESD0402-140
D904: MSS1P4-M3; MICROSMP; PARTNO MSS1P4-M3/89A
J901: HEADER-3X163X16RA; 3X16RA
L901: KNH16C104DA5TS; KYOCERA-KNH16-DA; PARTNO KNH16C104DA5TS
R901: 10K; 0402-RES; PARTNO RC0402FR-0710KL
R902, R903, R904, R905, R906, R907, R908, R909, R910, R911, R912, R913, R914, R915, R916, R917: 220R; 0402-RES; PARTNO RC0402FR-07220RL
R918, R919, R922: 10K/0.1%; 0402-RES; PARTNO ERA-2AEB103X
U901, U902: TXS0108QFN20; QFN20-RGY; PARTNO TXS0108ERGYR
U903: 74LVC2G240; TSSOP8_SOT505-2; PARTNO 74LVC2G240DP,125

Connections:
!SBUS_OUTPUT_EN: U903.7 (!2OE); also elsewhere on the board
FMU-CH1: U901.7 (A6); also elsewhere on the board
FMU-CH1-PROT: J901.46, R913.P$2 (2)
FMU-CH2: U901.6 (A5); also elsewhere on the board
FMU-CH3: U901.5 (A4); also elsewhere on the board
FMU-CH4: U901.4 (A3); also elsewhere on the board
FMU-CH5: U901.3 (A2); also elsewhere on the board
FMU-CH6: U901.1 (A1); also elsewhere on the board
FMU-CH6-PROT: J901.31, R902.P$2 (2)
FMU-VDD_3V3: C902.P$1 (1), U901.2 (VCCA), U901.10 (OE), U901.19 (VCCB); also elsewhere on the board
GND: C901.P$2 (2), C902.P$2 (2), C903.P$2 (2), D901.A, D902.A, D903.A, J901.3, J901.6, J901.9, J901.12, J901.15, J901.18, J901.21, J901.24, J901.27, J901.30, J901.33, J901.36, J901.39, J901.42, J901.45, J901.48, L901.P$3, L901.P$4, L901.P$5, R919.P$1 (1), U901.11 (GND), U902.11 (GND), U903.1 (!1OE), U903.4 (GND); also elsewhere on the board
IO-CH1: U902.9 (A8); also elsewhere on the board
IO-CH1-PROT: J901.28, R917.P$2 (2)
IO-CH2: U902.8 (A7); also elsewhere on the board
IO-CH3: U902.7 (A6); also elsewhere on the board
IO-CH4: U902.6 (A5); also elsewhere on the board
IO-CH5: U902.5 (A4); also elsewhere on the board
IO-CH6: U902.4 (A3); also elsewhere on the board
IO-CH7: U902.3 (A2); also elsewhere on the board
IO-CH8: U902.1 (A1); also elsewhere on the board
IO-CH8-PROT: J901.7, R905.P$2 (2)
IO-VDD_3V3: C901.P$1 (1), C903.P$1 (1), U902.2 (VCCA), U902.10 (OE), U902.19 (VCCB), U903.8 (VCC); also elsewhere on the board
IO-VDD_5V5: J901.2; also elsewhere on the board
unnamed: R918.P$2 (2), R922.P$1 (1)
unnamed: J901.10, R914.P$2 (2)
unnamed: D902.C, R901.P$2 (2), R910.P$1 (1), U903.3 (2Y)
unnamed: R905.P$1 (1), U902.20 (B1)
unnamed: R914.P$1 (1), U902.18 (B2)
unnamed: R906.P$1 (1), U902.17 (B3)
unnamed: R915.P$1 (1), U902.16 (B4)
unnamed: R907.P$1 (1), U902.15 (B5)
unnamed: R916.P$1 (1), U902.14 (B6)
unnamed: R908.P$1 (1), U902.13 (B7)
unnamed: R917.P$1 (1), U902.12 (B8)
unnamed: R902.P$1 (1), U901.20 (B1)
unnamed: R911.P$1 (1), U901.18 (B2)
unnamed: R903.P$1 (1), U901.17 (B3)
unnamed: R912.P$1 (1), U901.16 (B4)
unnamed: R904.P$1 (1), U901.15 (B5)
unnamed: R913.P$1 (1), U901.14 (B6)
unnamed: J901.34, R911.P$2 (2)
unnamed: J901.13, R906.P$2 (2)
unnamed: J901.16, R915.P$2 (2)
unnamed: J901.19, R907.P$2 (2)
unnamed: J901.22, R916.P$2 (2)
unnamed: J901.25, R908.P$2 (2)
unnamed: J901.37, R903.P$2 (2)
unnamed: J901.40, R912.P$2 (2)
unnamed: J901.43, R904.P$2 (2)
unnamed: J901.4, R910.P$2 (2)
unnamed: D903.C, D904.CATHODE (C), L901.P$1
PPM-SBUS-PROT: J901.1, R909.P$2 (2)
PPM_INPUT: D901.C, R909.P$1 (1), U903.2 (1A); also elsewhere on the board
RSSI_IN: R901.P$1 (1); also elsewhere on the board
SBUS_INPUT: U903.6 (1Y); also elsewhere on the board
SBUS_OUTPUT: U903.5 (2A); also elsewhere on the board
VDD_SERVO: D904.ANODE (A), J901.5, J901.8, J901.11, J901.14, J901.17, J901.20, J901.23, J901.26, J901.29, J901.32, J901.35, J901.38, J901.41, J901.44, J901.47, R922.P$2 (2); also elsewhere on the board
VDD_SERVO_IN: L901.P$2; also elsewhere on the board
VDD_SERVO_SENS: R918.P$1 (1), R919.P$2 (2); also elsewhere on the board

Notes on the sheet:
Servo Header S.Bus interface
S.Bus in/out
Servo outputs

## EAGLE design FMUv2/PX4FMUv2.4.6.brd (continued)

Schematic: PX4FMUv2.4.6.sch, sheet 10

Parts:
C1001: 10u/25V; 0805-CAP; PARTNO CL21A106KAYNNNE
C1002: 10n; 0402-CAP; PARTNO CC0402KRX7R7BB103
C1003: 1u; 0603-CAP; PARTNO CC0603ZRY5V7BB105
C1004: 10u; 0603-CAP; PARTNO C1608X5R1A106K080AC
C1005: 0u1; 0402-CAP; PARTNO CC0402ZRY5V7BB104
C1008: 2u2; 0402-CAP; PARTNO C1005X6S1C225K050BC
D1001: PMEG2005CT; SOT23-3; PARTNO PMEG2005CT
F1001: 0ZCA0035FF2G; PTC-1206; PARTNO 0ZCA0035FF2G
R1001: 100K; 0402-RES; PARTNO RC0402FR-07100KL
R1002: 10K; 0402-RES; PARTNO RC0402FR-0710KL
U1001: BQ24313; QFN8-DSG; PARTNO BQ24313DSGT
U1002: MIC5332; MLF-8-EPAD; PARTNO MIC5332-SSYMT

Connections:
GND: C1001.P$2 (2), C1002.P$2 (2), C1003.P$2 (2), C1004.P$2 (2), C1005.P$2 (2), C1008.P$2 (2), R1001.P$1 (1), R1002.P$1 (1), U1001.2 (VSS), U1001.5 (!CE), U1001.6 (VBAT), U1001.GND (VSS), U1001.P$2 (VSS), U1001.P$3 (VSS), U1002.2 (GND), U1002.GND; also elsewhere on the board
IO-!RESET: U1002.3 (POR2); also elsewhere on the board
IO-!VDD_SERVO_IN_FAULT: U1001.4 (!FAULT); also elsewhere on the board
IO-VDD_3V3: C1003.P$1 (1), C1004.P$1 (1), U1002.7 (VOUT2); also elsewhere on the board
IO-VDD_5V5: C1001.P$1 (1), C1005.P$1 (1), D1001.3 (CC), U1002.1 (VIN), U1002.4 (EN2); also elsewhere on the board
unnamed: D1001.2 (A2), U1001.8 (OUT)
unnamed: R1001.P$2 (2), U1001.7 (ILIM)
unnamed: D1001.1 (A1), F1001.2
unnamed: C1002.P$1 (1), U1002.6 (CSET)
VDD_3V3_SPEKTRUM: C1008.P$1 (1), U1002.8 (VOUT1); also elsewhere on the board
VDD_3V3_SPEKTRUM_EN: R1002.P$2 (2), U1002.5 (EN1); also elsewhere on the board
VDD_5V_IN: F1001.1; also elsewhere on the board
VDD_SERVO_IN: U1001.1 (IN); also elsewhere on the board

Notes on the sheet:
Dual supply from servo rail and FMU 5V rail
Current limit = 25 / Rilim (current in A, R in kOhms) 100K = 250mA
IO Power Supply
Reset output 1s / uF 10n = 10ms delay from power good to reset de-asserted.
Output voltage limited to 5.5V for input voltages up to 10.5V; output switches off at higher input voltages.

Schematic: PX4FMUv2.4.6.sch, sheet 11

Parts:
C1101, C1102, C1103: 22u/25V; 0805-CAP; PARTNO CL21A226MAQNNNE
C1104: 100u; 1206-CAP; PARTNO C3216X5R1A107M160AC
C1105, C1106, C1107: 0u1; 0402-CAP; PARTNO C1005X7R1E104K050BB
C1108, C1109, C1110: 10p/25V; 0402-CAP; PARTNO C0402C100J3GACTU
J601: DF13C-6P-1.25V; PARTNO DF13C-6P-1.25V(20)
L1101, L1102: KNH16C104DA5TS; KYOCERA-KNH16-DA; PARTNO KNH16C104DA5TS
R1101, R1102: 10K/0.1%; 0402-RES; PARTNO ERA-2AEB103X
R1103, R1104: 1M; 0402-RES; PARTNO RC0402FR-071ML
R1105, R1109, R1112: 453K; 0402-RES; PARTNO RMCF0402FT453K
R1106, R1110, R1113: 56K; 0402-RES; PARTNO ERA-2AEB563X
R1107, R1111, R1114: 105K; 0402-RES; PARTNO ERJ-2RKF1053X
R1115: 0R; 0402-RES; PARTNO ERJ-2GE0R00X
RN1101: 1M; EXB28V; PARTNO EXB-28V105JX
U1101: LTC4417; MO-220; PARTNO LTC4417IUF#PBF
U1102, U1103, U1104: NTHD4102PT1G; 1206-8; PARTNO NTHD4102PT1G

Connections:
!VBUS_VALID: RN1101.2 (1), U1101.P$9 (!VALID3); also elsewhere on the board
!VDD_BRICK_VALID: RN1101.4 (1), U1101.P$7 (!VALID1); also elsewhere on the board
!VDD_SERVO_VALID: RN1101.3 (1), U1101.P$8 (!VALID2); also elsewhere on the board
BATT_CURRENT_SENS: R1101.P$1 (1); also elsewhere on the board
BATT_CURRENT_SENS_PROT: J601.3, L1101.P$1, R1104.P$1 (1)
BATT_VOLTAGE_SENS: R1102.P$1 (1); also elsewhere on the board
BATT_VOLTAGE_SENS_PROT: J601.4, L1102.P$1, R1103.P$1 (1)
GND: C1101.P$2 (2), C1102.P$2 (2), C1103.P$2 (2), C1104.P$2 (2), C1105.P$2 (2), C1106.P$2 (2), C1107.P$2 (2), C1108.P$2 (2), C1109.P$2 (2), C1110.P$2 (2), J601.5, J601.6, L1101.P$3, L1101.P$4, L1101.P$5, L1102.P$3, L1102.P$4, L1102.P$5, R1103.P$2 (2), R1104.P$2 (2), R1107.P$2 (2), R1111.P$2 (2), R1114.P$2 (2), R1115.P$1 (1), U1101.P$10 (GND), U1101.P$25 (GND); also elsewhere on the board
unnamed: C1108.P$1 (1), R1105.P$2 (2), R1106.P$1 (1), U1101.P$1 (UV1)
unnamed: R1106.P$2 (2), R1107.P$1 (1), U1101.P$2 (OV1)
unnamed: C1109.P$1 (1), R1109.P$2 (2), R1110.P$1 (1), U1101.P$3 (UV2)
unnamed: R1110.P$2 (2), R1111.P$1 (1), U1101.P$4 (OV2)
unnamed: R1113.P$2 (2), R1114.P$1 (1), U1101.P$6 (OV3)
unnamed: C1110.P$1 (1), R1112.P$2 (2), R1113.P$1 (1), U1101.P$5 (UV3)
unnamed: C1105.P$1 (1), U1101.P$18 (VS1), U1102.P$1 (S), U1102.P$3 (S)
unnamed: L1102.P$2, R1102.P$2 (2)
unnamed: L1101.P$2, R1101.P$2 (2)
unnamed: R1115.P$2 (2), U1101.P$24 (HYS)
unnamed: C1106.P$1 (1), U1101.P$16 (VS2), U1103.P$1 (S), U1103.P$3 (S)
unnamed: C1107.P$1 (1), U1101.P$14 (VS3), U1104.P$1 (S), U1104.P$3 (S)
unnamed: U1101.P$13 (G3), U1104.P$2 (G), U1104.P$4 (G)
unnamed: U1101.P$15 (G2), U1103.P$2 (G), U1103.P$4 (G)
unnamed: U1101.P$17 (G1), U1102.P$2 (G), U1102.P$4 (G)
VBUS: C1103.P$1 (1), R1112.P$1 (1), U1101.P$19 (V3), U1104.P$7 (D), U1104.P$8 (D); also elsewhere on the board
VDD_5V_BRICK: C1101.P$1 (1), J601.1, J601.2, R1105.P$1 (1), U1101.P$21 (V1), U1102.P$7 (D), U1102.P$8 (D); also elsewhere on the board
VDD_5V_IN: C1104.P$1 (1), RN1101.5 (2), RN1101.6 (2), RN1101.7 (2), U1101.P$12 (VOUT), U1102.P$5 (D), U1102.P$6 (D), U1103.P$5 (D), U1103.P$6 (D), U1104.P$5 (D), U1104.P$6 (D); also elsewhere on the board
VDD_SERVO: C1102.P$1 (1), R1109.P$1 (1), U1101.P$20 (V2), U1103.P$7 (D), U1103.P$8 (D); also elsewhere on the board

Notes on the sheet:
Power source selector
Resistors picked so that undervoltage lockout starts at 4.0V and overvoltage lockout at 5.75V. Use 1% or better accuracy!
POWER PATH CONTROLLER: Does enable output if valid for continous 256 ms
XXX Check all input pins are 5V tolerant. Hooking this up to a 3.3V rail would make the lines non-readable during power-up sequencing

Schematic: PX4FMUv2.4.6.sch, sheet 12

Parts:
!VBUS_VALID: PAD.04; PAD.04X.04; PARTNO *
!VDD_BRICK_VALID: PAD.04; PAD.04X.04; PARTNO *
!VDD_SERVO_VALID: PAD.04; PAD.04X.04; PARTNO *
ADC_PR: PAD.04; PAD.04X.04; PARTNO *
CAN_H: PAD.04; PAD.04X.04; PARTNO *
CAN_L: PAD.04; PAD.04X.04; PARTNO *
FMU-BOOT1101: PAD.04; PAD.04X.04; PARTNO *
GND, GND.: PAD.04; PAD.04X.04; PARTNO *
IO-BOOT1101: PAD.04; PAD.04X.04; PARTNO *
JP1, JP2: FIDUCIAL1.5X3; FIDUCIAL-1.5X3; PARTNO *
M3_MOUNT1101, M3_MOUNT1102, M3_MOUNT1103, M3_MOUNT1104: MOUNT-HOLE3.1MM; MOUNT-HOLE3.1; PARTNO *
OSHW_LOGO: OSHW-LOGOS; OSHW-LOGO-S; PARTNO *
S1RX, S1TX, S2RX, S2TX, S3RX, S3TX, S4RX, S4TX, S5_RX, S5_TX: PAD.04; PAD.04X.04; PARTNO *
VBUS: PAD.04; PAD.04X.04; PARTNO *
VDDA_3V1101: PAD.04; PAD.04X.04; PARTNO *
VDD_3V1101, VDD_5V_BRICK, VDD_5V_IN: PAD.04; PAD.04X.04; PARTNO *
VDD_SERVO: PAD.04; PAD.04X.04; PARTNO *

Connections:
!VBUS_VALID: !VBUS_VALID.P$1; also elsewhere on the board
!VDD_BRICK_VALID: !VDD_BRICK_VALID.P$1; also elsewhere on the board
!VDD_SERVO_VALID: !VDD_SERVO_VALID.P$1; also elsewhere on the board
CAN_H: CAN_H.P$1; also elsewhere on the board
CAN_L: CAN_L.P$1; also elsewhere on the board
FMU-BOOT0: FMU-BOOT1101.P$1; also elsewhere on the board
FMU-VDD_3V3: VDD_3V1101.P$1; also elsewhere on the board
GND: GND.P$1, GND..P$1; also elsewhere on the board
IO-BOOT0: IO-BOOT1101.P$1; also elsewhere on the board
PRESSURE_SENS_IN: ADC_PR.P$1; also elsewhere on the board
SERIAL1_RX: S1RX.P$1; also elsewhere on the board
SERIAL1_TX: S1TX.P$1; also elsewhere on the board
SERIAL2_RX: S2RX.P$1; also elsewhere on the board
SERIAL2_TX: S2TX.P$1; also elsewhere on the board
SERIAL3_RX: S3RX.P$1; also elsewhere on the board
SERIAL3_TX: S3TX.P$1; also elsewhere on the board
SERIAL4_RX: S4RX.P$1; also elsewhere on the board
SERIAL4_TX: S4TX.P$1; also elsewhere on the board
SERIAL5_RX: S5_RX.P$1; also elsewhere on the board
SERIAL5_TX: S5_TX.P$1; also elsewhere on the board
VBUS: VBUS.P$1; also elsewhere on the board
VDD_3V3_SENSORS: VDDA_3V1101.P$1; also elsewhere on the board
VDD_5V_BRICK: VDD_5V_BRICK.P$1; also elsewhere on the board
VDD_5V_IN: VDD_5V_IN.P$1; also elsewhere on the board
VDD_SERVO: VDD_SERVO.P$1; also elsewhere on the board

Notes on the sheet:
Mounting holes to suit M3 fastener
and Richco R908 series spacer.
Use R908-5 spacers to stack with
other PX4 series boards (7.95 mm).
Production Testing Pads
Test and Fiducials
Minimum drill: 0.3 mm
Minimum trace width (use mm for traces): 0.15 mm
Minimum copper distance (all signals): 0.15 mm
Dimension / hole minimum distance: 0.2 mm
Layout grid: 4 mil, part grid: 4 mil. Dimensions / hole positions: 0.5 mm
Board: FR4 black, 1.0 mm. Solder stop on vias < 0.6 mm.
Signoff rules: Footprint checked, pinmap checked, schematic checked, cross-references to other pages checked.
Routing: 1: general/escape 2: ground 3: horizontal 4: vertical 5: power 6: general/escape
Fiducials for machine vision alignment.
Parts: Resistors: 0402 / 1% unless specified otherwise Capacitors: 0402 to 1206, ceramic, voltage rating: 10V unless specified
COMMS
POWER
STATUS AND ANALOG

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

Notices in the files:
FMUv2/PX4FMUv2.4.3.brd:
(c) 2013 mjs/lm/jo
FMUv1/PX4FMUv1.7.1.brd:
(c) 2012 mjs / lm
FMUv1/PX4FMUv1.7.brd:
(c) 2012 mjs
